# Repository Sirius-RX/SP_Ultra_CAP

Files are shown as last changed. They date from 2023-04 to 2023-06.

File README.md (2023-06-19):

# SP_Ultra_CAP

### 目录

[SP\_Ultra\_CAP](#sp_ultra_cap)

- [目录](#目录)
- [项目所属：河北工业大学\_山海Mas战队	Sirius\_P](#项目所属河北工业大学_山海mas战队sirius_p)
- [最后更新时间：2023.6.19](#最后更新时间2023619)
- [每个文件夹下面都有独立的readme，用以解释目录内容](#每个文件夹下面都有独立的readme，用以解释目录内容)
- [文件目录](#文件目录)
- [简介](#简介)
    - [测试视频：【Robomaster超级电容功能展示（默剧）（最高集成度\&较低成本）】](#测试视频robomaster超级电容功能展示默剧最高集成度较低成本)
    - [外设一览：](#外设一览)
    - [以下为渲染预览图，使用渲染软件keyshot](#以下为渲染预览图使用渲染软件keyshot)
    - [实物焊接图（因为喷了三防漆可能有点影响观感）](#实物焊接图因为喷了三防漆可能有点影响观感)
    - [**项目方案优点**](#项目方案优点)
    - [**项目方案缺点**](#项目方案缺点)
- [硬件框图](#硬件框图)
- [软件框图](#软件框图)

### 项目所属：河北工业大学_山海Mas战队	Sirius_P

	我们是于2022年成立，2023年第一次参赛的新战队，还请各位大佬们多多指教。

### 最后更新时间：2023.6.19

2023.6.19	优化CAN发送&接收程序，功能上加上了缓冲功率的使用，默认锁死在20J；

2023.6.3    更新CAN发送&接收程序；

2023.5.31    更新原理图的采样电阻阻值；

2023.4.29	初始化工程，上传了HARDWARE内容和MATLAB内容，初步完成主页面readme；

2023.4.30	更新了部分设计报告内容（要死了，天天做工）；

2023.5.1	更新Doc中readme，更新SOFTWARE中readme，更新HARDWARE中readme，更新设计报告内容，上传了框图源文件，上传源代码；

2023.5.2	更新部分文档中的错别字；

### 每个文件夹下面都有独立的readme，用以解释目录内容

### 文件目录

**请移步文件目录.txt**

### 简介

##### 	测试视频：[【Robomaster超级电容功能展示（默剧）（最高集成度&较低成本）】](https://www.bilibili.com/video/BV1DM4y127du/?share_source=copy_web&vd_source=c66b5cf402383e929f3b27696605cd3c) 

	该项目用作于Robomaster电容管理，使用单板在7.62cm* 7.62cm*2.5cm（高度主要是有个EC11旋钮有点小高）的超小体积下实现了集成度较高的双向buckboost控制，系统的响应频率高达200kHz。

##### 	外设一览：

-   IPS屏幕接口
-   EC11旋钮
-   蜂鸣器
-   RGB灯（三路PWM控制）
-   两路FDCAN通信
-   ICM42605陀螺仪

##### 	以下为渲染预览图，使用渲染软件keyshot

	

	

##### 	实物焊接图（因为喷了三防漆可能有点影响观感）

	

	

##### **项目方案优点**	

1.  工作模式能在buck、buck-boost、boost三种不同的工作拓扑之间进行无感切换，使得电路工作效率最大化；
2.  超高集成度，在保证体积的前提下，集成了诸多外设及其电调中心板的功能，使得底盘只需要两个pcb即可实现所有功能，节省了底盘的安装空间；
3.  超多外设使得开发板的功能能在后续工程的推进可以增加更多的功能；
4.  6层板设计，叠层结构：电源-模拟地（包括电源地）-电源-信号-数字地-信号，设计时正面器件只有功率与模拟器件，背面器件只有数字器件，使得pcb设计中所有的地回路均为最短且具有两个完整的参考地平面。两个地之间使用了一个680R@100MHz/4A的磁珠进行单点连接；
5.  在同类方案中最低的成本：电流采样运放使用NCS210RMUTAG（全新2.8774yuan一片，云汉芯城2023.1.19报价，现在好像涨了），电压跟随运放使用NCS20282FCTTAG（两路运放，全新4.61yuan一片，e络盟2023.1.17报价），桥驱使用ADP3110AKCPZ-RL（全新3.43yuan一片，e络盟2023.1.17报价），MOS使用国产HYG025N06LS1C2（60V/170A 全新4.11yuan一片，立创2023.4.29报价），电感使用国产TMPC1707HP-100MG-D（10uH/16.5A/11.8mΩ 全新7.1yuan一片，立创2023.4.29报价）。上述都是buckboost实现的核心组件，也是各大学校最堆料的一些组件，选型仅供参考，报价均按1个购买价格计算，并非梯度价格；
6.  极高的控制频率：PWM控制频率200k，让你体验几乎瞬时的功率响应，实现方式请移步SOFTWARE readme；
7.  拥有众多保护功能，包括不限于：输入过压保护，输入掉压保护，输出过流保护，输出过压保护等；
8.  *这一块板子没有经过任何迭代，初版即为最终版。

##### 	**项目方案缺点**

1.  电流采样使用了采样滤波电路，导致电流采样放大后的电压有线性误差，每个板子需要单独校准电流参数；

### 硬件框图

**使用drawio绘制，HTML（高清矢量图）请移步Doc文件夹**



### 软件框图

**使用drawio绘制，HTML（高清矢量图）请移步Doc文件夹**

软件框图是当时给自己提供代码功能设计思路用的，实际实现的方式可能与框图中有些不一样（PS：因为框图是写代码之间先画的，所以肯定会和实现差比较多，因为我是懒狗就还没更新，等后续有时间了再更新一下）



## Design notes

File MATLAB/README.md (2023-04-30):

# SP_Ultra_CAP

### 目录内容

此文件夹用以存放Simulink仿真文件

### 文件简介

buck_boost.slx：电路buck工作模式时的仿真文件

buck_boost_mix.slx：电路buck-boost工作模式时的仿真文件

### 文件使用环境

Matlab 2023a

### 文件使用方法

文件主要是用来验证设计合理性和调整PID参数，PID参数调整方法如下：

1.  先将系统中输出的变量调整至由一个PID环决定；
2.  选中Simulink库中的PID模型并点开；
3.  打开后点击自动调节栏目中的调节按钮（注意调节方式选择基于频率相应）；
4.  配置好对应的参数之后点击调节，具体参数的含义及其配置方式可以参考Matlab官方教程，链接如下：[Design PID Controller Using Plant Frequency Response Near Bandwidth - MATLAB & Simulink - MathWorks 中国](https://ww2.mathworks.cn/help/slcontrol/ug/design-pid-controller-using-plant-frequency-response-near-bandwidth.html)；
5.  在上述自动调整器输出的结果上微调，直至达到自己认为的理想情况。

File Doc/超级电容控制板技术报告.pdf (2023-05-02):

## 基于 STM32G474 的超级电容控制器

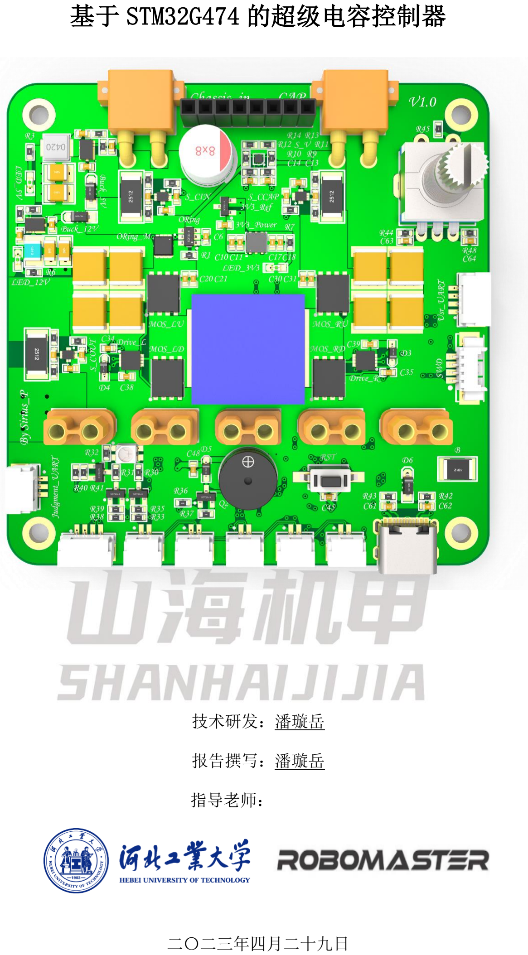
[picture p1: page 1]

技术研发：潘璇岳

报告撰写：潘璇岳

指导老师：

二〇二三年四月二十九日

基于 STM32G474 的超级电容控制器
摘要

针对 Robomaster 赛事中限制兵种底盘功率的规则，本战队制作了一款能够自动控制底

盘输出功率，并合理利用输出功率的超级电容控制器。本设计中的硬件部分主要由一个双向

BUCK-BOOST 变换器及其控制电路构成。包括微控制单元（MCU）、信号采样电路、主拓扑结

构及 MOS 驱动电路、辅助电源电路、传感器电路等。由 MCU 控制输出两路宽度调制的脉冲信

号（PWM）来控制 H 桥中各个 MOS 管导通时间的变化；同时，信号采样电路对输出和输出信

号进行采样，并将其传输给 MCU 来调节系统。系统主要通过 PID 算法来控制功率、电流以及

电压的闭环，更新频率高达 200kHz。经调试，本系统可以根据输出电压，自动变换工作的

拓扑，在 buck 和 buck-boost 工作模式中自由切换，并且在各种情况下都保证输入功率稳

定，最大功率输出可达到 300W。

关键词：超级电容控制器；DC-DC 变换器；PID 算法；

### Abstract

In response to the Robomaster competition's rule that limits the power of certain chassis types,

our team has developed a controller that can automatically regulate the output power of the chassis

and make efficient use of a supercapacitor. The hardware component of this design primarily

consists of a bidirectional buck-boost converter and its control circuitry, including a microcontroller

unit, signal sampling circuit, main topology structure and MOS driver circuit, auxiliary power

circuit, and sensor circuit. The MCU controls the pulse width modulation (PWM) signals that

modulate the on-time of each MOS in the H-bridge to regulate the output power. At the same time,

the signal sampling circuit samples the output and output signals and transmits them to the MCU to

adjust the system. The system mainly employs a closed-loop PID algorithm to control power,

current, and voltage. Through debugging, the system can automatically switch between buck and

buck-boost modes according to the output voltage and ensure stable input power in various

situations. The maximum power output can reach 300W.

Keywords: super capacitor controller; DC-DC converters；PID algorithm

目录

## 1 方案论证

超级电容控制器的硬件主要由一个双向 BUCK-BOOST 变换器构成，裁判系统功率输入经

过理想二极管后与双向 BUCK-BOOST 变换器并联，最后能够与电容放电回路一起输出功率到

负载上。通过改变双向 BUCK-BOOST 中左侧与右侧上管 MOS 给电感的充电时间，可以实现电

流正反向的控制。在系统的调控下，无论输出负载功率如何变化，裁判系统输入功率、能量

缓冲仍符合规则要求，保持稳定。

1.1 | 主控单元的比较与选择
| 方案一：选择数字电源主流方案，使用 TI 旗下的 DSP 芯片作为数字电源控制器，如

TMS320F280x 系列、TMS320F2801x 系列，还有可输出 16 通道高精度 PWM 的 DSP 处理器

TMS320F28044。这些 DSP 处理器开发需要专有的 IDE 并要熟悉其独特的开发方式，学习成本

较高，可能使得工程开发周期较长。

| 方案二：采用 STM32G4 系列。该系列单片机拥有 5 个能达到 4Msps 的 12bit ADC 外设，

外设中使用了专门的加法器电路来实现硬件过采样功能，可以在很大程度上减轻 CPU 负担，

在 ADC 过采样工作模式中可达到 16bit 的精度；有 6 个片上的高速、高增益带宽运算放大器；

7 个能达到 1Msps 的 12 位 DAC（内部输出的话可以达到 15Msps），满足了超级电容控制器

需要精准测量电压电流的需求，同时其 170MHz 的较高主频能有效的提高环路的控制频率。

| 其 HRTIM（高分辨率和复杂波形生成器）外设拥有 6 个独立的 16 位计数器，该计数器

最高能达到 184 ps 的精度，可以生成互补 PWM 波并带有死区控制功能，满足了双向 BUCK-

BOOST 变换器要精准控制 MOS 管导通时间的需求。

| 同时其拥有的 FMAC（数学滤波加速器）外设能够使得 FIR 滤波器或者 IIR 滤波器的计

算完全独立于 CPU，能实现较好的滤波性能同时降低 CPU 的算力开销。

| 但是其价格在贸泽上一片需要 100 多元（2022.12.18，现在淘宝一片也就 40 出头），

实现批量生产成本较高。

| 方案三：采用 STM32F3 系列。该系列单片机具有超快速比较器（25 ns）和可编程增益

的运算放大器。12 位 DAC 以及超快速 12 位 ADC，每通道每秒 5 MSPS（每秒百万次采样），

该系列芯片主频为 72MHz，比 G4 系列的一半还少。虽然其基本满足了超级电容控制器需要

精准测量电压电流的需求，但是在代码实现中较多的计算将会降低系统的实时性。

| 其拥有的 144 MHz 高级 16 位脉宽调制定时器（分辨率 <7ns），可以用于生成互补 PWM

波并有死区控制功能，也基本满足了双向 BUCK-BOOST 变换器要精准控制 MOS 管的需求。

综上所述，选择方案二。

### 1.2 功率检测方式的比较与选择 方案一：数字电流/功率监控器。使用如 INA231 等数字电流/功率监控器，可以通过一

个芯片同时实现双向电流、节点电压以及功率的采集，从而获得校准级别的测量精度以及超

低温漂。这类芯片大多使用I

| 2C通信协议与 MCU 进行数据传输，它在采集完电压电流数值的

同时，能通过内部硬件电路完成功率的计算，并且能直接将该功率数据通过I

2C接口传输给

MCU，能够节省很大一部分的算力开销。同时，这类芯片也可以通过I

2C的配置通过内部硬件

电路完成各个采样值的取平均（等效于低通滤波），也可以编程一个警报阈值，直接通过一

个引脚的高低电平来判断功率是否超过设定值。上述的这些功能在设计上能够将大部分采样、

计算与滤波这些本来应该在 MCU 上完成的功能在传感器芯片上完成，这将能够极大的解放

CPU 的算力，使得系统的响应速度能够更上一层，或者能够将多余的算力来完成其它功能的

设计。尽管如此，这类传感器芯片有几个致命的缺点：1.笔者遍历了 ADI 和 TI 公司的此类

芯片，他们的采样频率基本都不能超过 30kHz，再算上滤波对于采样频率的开销，根据采样

定理可得系统的控制频率也不能超过 30kHz；2.此类芯片一般价格高昂，对于我们这种经济

实力不怎么强的战队来说是一个很大的负担。

| 方案二：运放采样电流电压。通过采样电阻加差模放大器的经典电流采样电路来实现电

流采样。这样的方案相对于上面的方案来说，需要自己编写程序计算功率，同时还要设计好

运放的外部电路。运放采样对于 MCU 来说，在运放端和 MCU 的模拟端均需要一个足够精准且

电流能够快速变化的基准电压源，对于电路设计来说也就需要一个额外的基准电压源电路，

如果想要采样双向电流的话要又额外需要一个独立的电源电压来提供基准电压，这将使得设

计进一步复杂。不过可以通过加一路输出电流采样，通过输入减输出的方式来计算反向电流

的方法来简化设计以及成本。相对于方案一来说，方案二中使用的运放芯片成本较低。

| 综上所述，选择方案二。
1.3 | 系统电路的比较与选择 方案一：裁判系统与电容通过功率路径管理后向底盘供电 当底盘所需功率小于裁判系统所能提供的最大功率时，裁判系统的功率路径被选中打开，

电容组升压的功率路径被关闭，同时，根据官方主控传回的实时输出功率，数字同步 BUCK

模块可以精确设定给电容组充电的功率（即电流）。当底盘所需功率大于裁判系统所能提供

的最大功率时，裁判系统的功率路径被关闭，电容组升压的的功率路径被选中打开，同时，

数字同步 BUCK 模块将裁判系统所能提供的最大功率全给电容充电，电容组通过自主设计的

具有恒压功能的 LM5122 升压模块，向底盘供电，从而保证输出电压恒定，不会烧掉电调或

低压保护。同时数字同步 BUCK 电源可以精确设定给电容充电的功率，利于实现功率闭环。

功率路径管理是由每路电源串联背对背 NMOS 开关，通过 LM5060 功率控制器实现主动式

功率路径管理，实现主动切换输出电路。而输入功率检测是通过电阻串联分压后由 MCU 的

ADC 直接获得输入电压，采用基于霍尔原理的电流传感器高端采集输入电流（电压电流对应

乘积即为功率值）。

但是，当底盘所需功率大于裁判系统所能提供的最大功率时，系统会存在两级 DC-DC 变

换器，总效率由于为两级效率乘积而特别低。根据官方主控传回的实时输出功率，不仅存在

一定的延时性，而且当电容电压越低时，输入输出电压压差较大，系统效率也会随之降低。

功率路径管理为两路背对背 NMOS 开关，在 NMOS 上有一定的能量损耗。设计中并未做到电机

反动势能量回收，而是将其损耗在 TVS 管上。

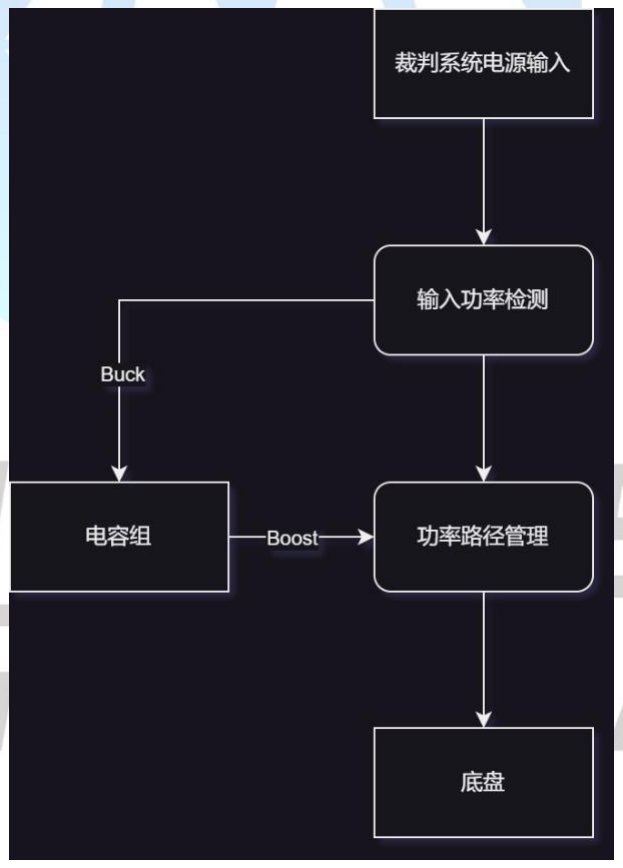
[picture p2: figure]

图 1 系统方案 1 框架简图
方案二：裁判系统通过理想二极管与电容通过双向 DCDC 向底盘供电

当底盘所需功率小于裁判系统所能提供的最大功率时，根据电池端口测量电压、电流得

到的实时输出功率，数字双向 DC-DC 可以精确设定给电容组充电的功率。当底盘所需功率大

于裁判系统所能提供的最大功率时，数字双向 DC-DC 将电容组升高电压，与裁判系统一起向

底盘供电。通过调节数字双向 DC-DC 及电容组的输出功率，我们可以保证裁判系统能量缓冲

稳定在我们预先设置的数值上下浮动，从而实现了能量缓冲的闭环。

输入输出功率都是用运算放大器进行间接测量：运算放大器将电压等比例缩放至

0~3.3V，也就是 ADC 测量范围内，再由单片机 ADC 引脚进行采集；在双向 DCDC 的输入和输

出均放置1mΩ的采样电阻，同样再用一个1mΩ的采样电阻放在电流流入底盘的一端，采样电

阻两端产生的差分电压通过差分运放放大至一个合理范围内之后被单片机 ADC 引脚采集，经

过对应的电压电流计算式，我们可以换算得到真实的电压、电流值，然后通过大名鼎鼎的

P = U × I公式就能得到功率值。此数据具有实时性，所以在闭环中更有优势。

由于系统只存在一级 DC-DC 变换器（可以工作在 buck、buck-boost 或者 boost 三种拓

扑下），对比方案一，该方案总效率为单级效率，效率可得到一定提升。同时，该系统可实

现电机反动势能量的回收。

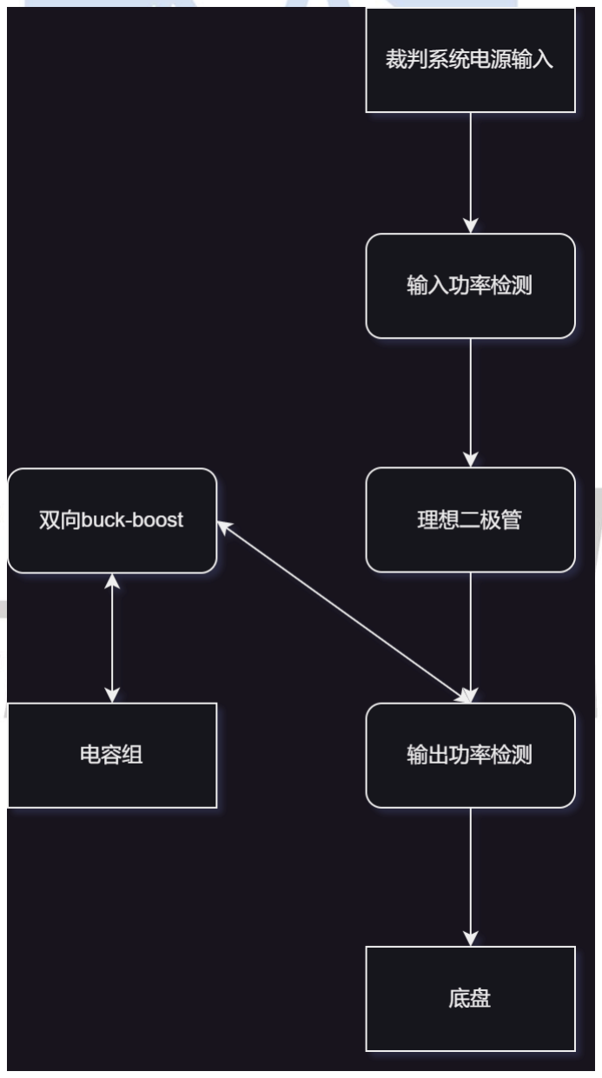
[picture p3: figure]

图 2 系统方案 2 框架简图

综上所述，选择方案二。

### 1.4 方案描述

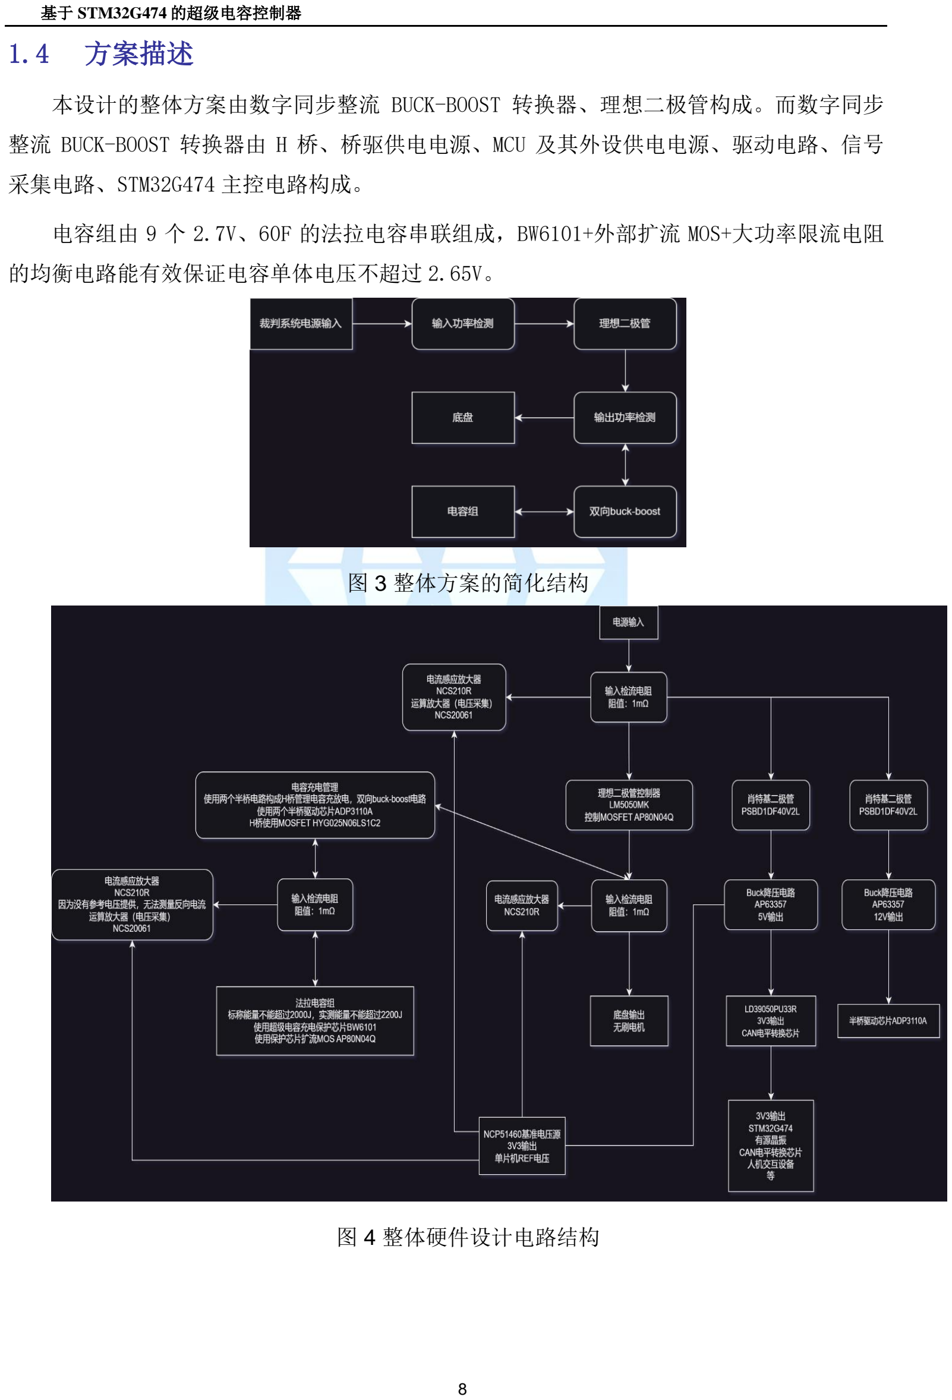
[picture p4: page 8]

本设计的整体方案由数字同步整流 BUCK-BOOST 转换器、理想二极管构成。而数字同步

整流 BUCK-BOOST 转换器由 H 桥、桥驱供电电源、MCU 及其外设供电电源、驱动电路、信号

采集电路、STM32G474 主控电路构成。

电容组由 9 个 2.7V、60F 的法拉电容串联组成，BW6101+外部扩流 MOS+大功率限流电阻

的均衡电路能有效保证电容单体电压不超过 2.65V。

图 3 整体方案的简化结构

图 4 整体硬件设计电路结构

## 2 理论分析与计算

2.1 | DC-DC 变换器提高效率的方法
| DC-DC 变换器效率提升技术主要集中在两个方面：拓扑结构、器件以及控制策略。 拓扑结构及器件上的改进：用 MOSFET 替代经典 BUCK-BOOST 拓扑中的续流二极管，以减

少在其上的压降与功率损耗；同时，选用RDS(on)较小的 MOSFET 和阻值较小的电感以减少导

通损耗；系统电路中尽量减少 DC-DC 转换器数目，保证 DC-DC 变换器两端的输入、输出压差

处在合适范围[3]。

| 控制策略的改进：通过正确设置 MOSFET 开关频率，以减小功率器件开通与关断状态切

换所引起的开关损耗；同时系统会根据输入与输入的电压差，自动判断最优的工作拓扑模式，

例如：在输出电压低于输入电压是右桥上管长时间导通，左桥上下管循环导通，让电路工作

在 buck 模式；在输出电压接近于输入电压时使用 buck-boost 工作模式，这样相对于只用

buck-boost 一个工作模式来说，效率能够得到进一步提高。

2.2 | BUCK-BOOST 控制策略
| 双向同步整流 BUCK-BOOST 电路由同步 BUCK 电路和同步 BOOST 电路级联而成，根据

BUCK 电路电压增益公式：Uo

| Ui = DBU，和 BOOST 电路电压增益公式：Uo
Ui

=

1
1−DBO

推出 BUCK-

BOOST 电路电压增益公式：Uo

| Ui = DBU 1−DBO ，其中DBU定义为 BUCK 电路的占空比，对应本设计中

MOS 管 Q1 的占空比，DBO定义为 BOOST 电路的占空比，对应本设计中 MOS 管 Q4 的占空比。

本设计中 Q1 和 Q2 是一对互补导通 MOS 管，Q3 和 Q4 是一对互导通 MOS 管。双向同步整

流 BUCK-BOOST 电路根据输入输出的电压关系将电路工作状态分为降压区、升压区和降压-升

压区；当输出电压显著小于输入电压时，电路工作在降压区，此时 Q1 和 Q2 互补导通，Q4

常关 Q3 常通，电路等效于同步 BUCK 电路；实际应用中由于 MOS 管驱动采用自举升压的方式，

Q4 不能始终截止，否则当 Q3 的自举电容能量损耗完时，Q3 将截止；为驱动 Q3，Q4 必须导

通一小段时间为 Q3 的自举电容充电以驱动 Q3。因此在实际控制中可将 Q4 的占空比固定设

为 0.75（即DBO可根据实际情况调整），而 Q1 的占空比DBU可在0~0.95之间变化，如此电

路将一直工作在降压区。当输出电压显著大于输入电压时，电路工作在升压区，等效于同步

BOOST 电路，和电路工作在降压区的情况类似，Q2 不能始终截止，需要导通一小段时间为

Q1 的自举电容充电，因此在实际控制中可将 Q1 的占空比DBU固定设置为 0.95（可根据实际

情况调整），而 Q4 的占空比可在0~0.95之间变化，如此电路将一直工作在升压区。当输出

电压和输入电压接近时，电路工作在降压-升压区，即在一个周期内一段时间按降压方式工

作，一段时间按升压方式工作。双向同步整流 BUCK-BOOST 电路 MOS 管开关状态主要有如图

5 所示三种状态。

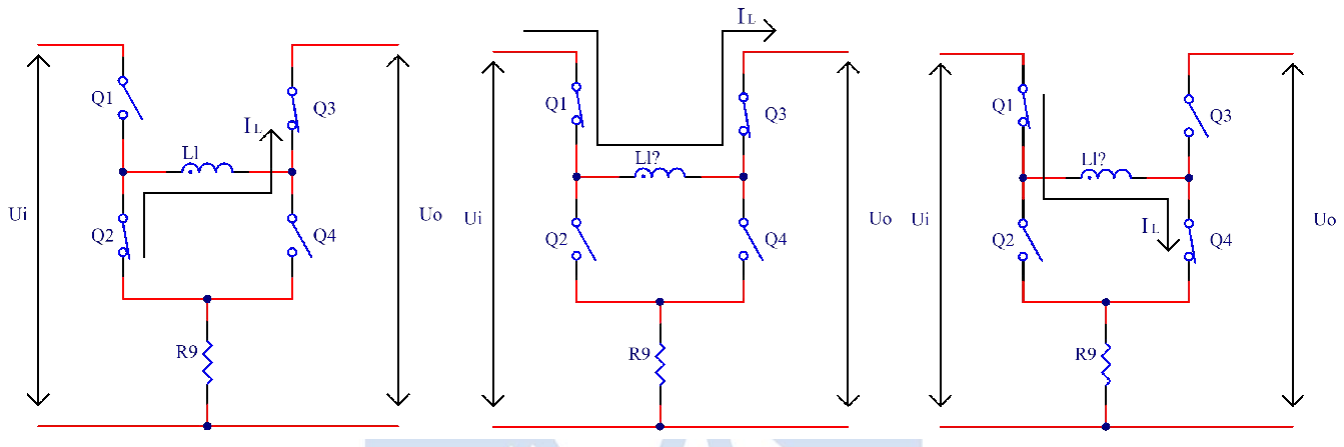
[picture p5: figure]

图 5 MOS 管开关状态

当 MOS 管在 A、B 状态之间切换时，电路工作在降压模式；当 MOS 管在 B、C 状态之间切

换时，电路工作在升压模式；当 MOS 管按照状态 A-B-C-B-A 的顺序切换时，电路工作在降压

-升压模式。如图 6 所示为电路工作在降压-升压模式时的驱动波形和电感电流波形。

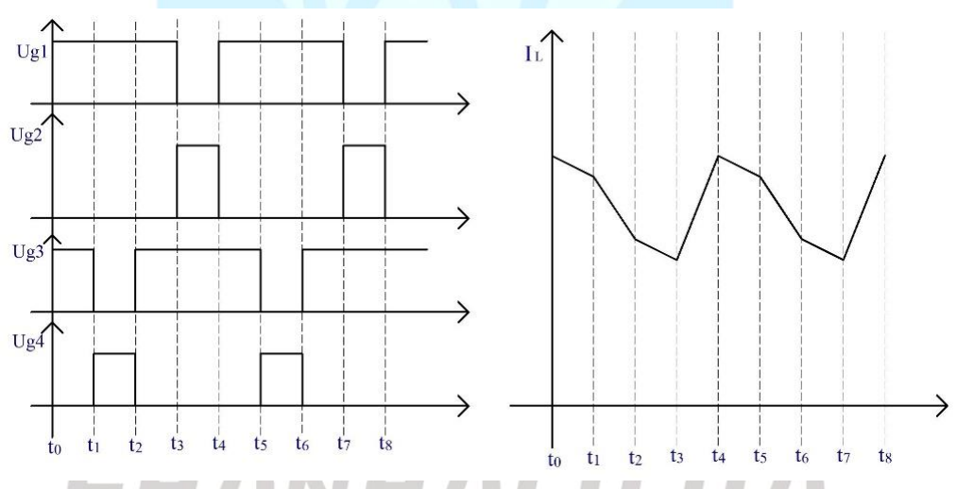
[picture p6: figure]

图 6 降压-升压模式下的驱动波形和电流波形

在t0 − t1阶段电路处于状态 B，此时 Q1、Q3 导通，Q2、Q4 截止；当Ui>Uo时，电感电流

增大；

当Ui < Uo时，电感电流减小。在t1 − t2阶段电路处于状态 C，此时 Q1、Q4 导通，Q2、

Q3 截止，电感电流增大。在t2 − t3阶段电路处于状态 B，在t3 − t4阶段电路处于状态 A，此

时 Q2、Q3 导通，Q1、Q4 截止，电感电流减小。由 BUCK-BOOST 电压增益公式可知，不论电

路是工作在降压模式、升压模式还是降压-升压模式，本质上是控制降压占空比DBU和升压

占空比DBO。

## 3 电路与程序设计

3.1 | DC-DC 变换器主电路与器件选择
| DC-DC 变换器主电路器件为 N 沟道场效应管 HYG025N06LS1C2，驱动芯片 ADP3110AKCPZ-

RL，一体成型电感，插针固态电容和陶瓷电容（MLCC）。

### 3.1.1 DC-DC 变换器主电路设计

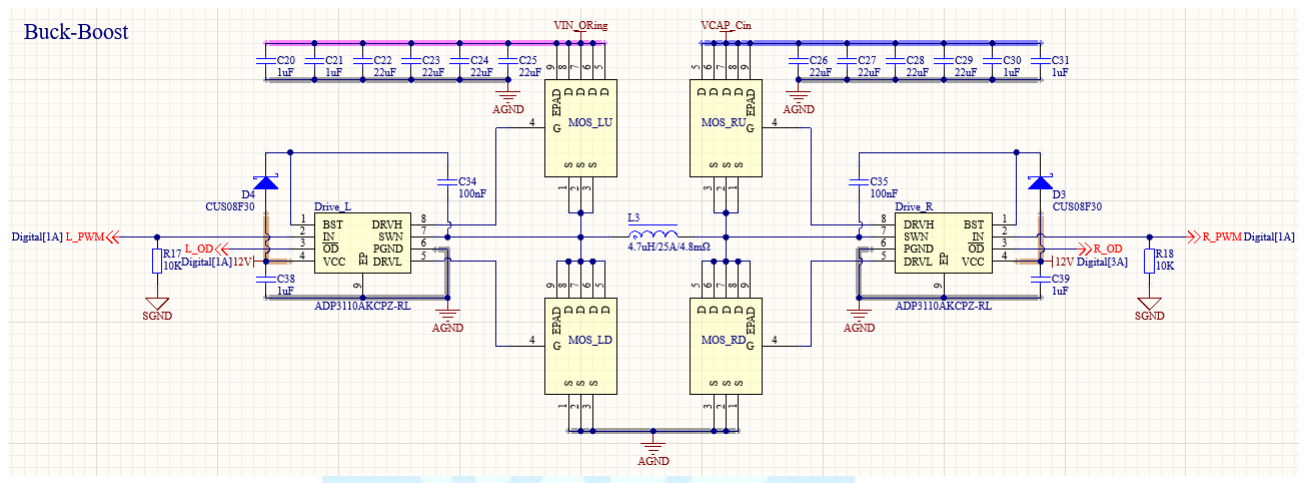
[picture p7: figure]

图 7 双向 BUCK-BOOST 拓扑
由 BUCK-BOOST 参数计算公式可知：纹波系数取 0.3

BUCK 模式需要电感大小：L =

(Vinmax−Vout)D

0.5f×I0utMAX

=

26.2−1
200000×0.3×15

×

1
26.2

= 1.07uH,

BOOST 模 式 下 需 要 电 感 大 小 ： L =

k×Vout(1−D)

2D

2f×I0utmax×10%

=

26.2
200000×2×15×10%

× (

25.2
26.2

)

2 ×

1
26.2

=

6.52uH，

在两种情况取较大的电感值，且留有余量，所以电感 L 取值 10uH。

由于该电路双向对称，所以输入电容和输出电容需要相同容量：

输出最大纹波电压∆UO = 26.2 ∗ 0.3% = 0.0786V,由于使用的固态电容的 ESR 较小，计

算中忽略不计，计算电容充电引起的电容纹波。则所需电容的容值：

C =

∆I
f×∆UO×2

=

0.3×15
200000×0.0786×2

= 143.13uF

输入输出电容要大于143.13uF，不过我们的设计要留有余量。并且需要考虑电机会产

生较大的反生电动势，需要额外的电容来吸收，防止电压的突变。所以最终方案每个半桥的

电源端采用 2 个 1uF/50V X5R、2 个 22uF/50V X7R 和一个 1000uF/35V 8mΩ的固态电容。

### 3.1.2 驱动电路及 MOSFET

MOS 管驱动器采用 onsemi 具有独立的高侧和低侧驱动的半桥驱动芯片 ADP3110A，该

芯片价格低廉，有能够自动产生死区时间的硬件电路，也就是说只需要一路 PWM 便可以控制

一个半桥，简化了控制逻辑。芯片没有集成自举二极管，需要在外部连接自举电容以及充电

二极管，采用自举升压的方式驱动高侧 MOS 管。为了优化效率，这边使用了 30V 1A

230mV@100mA 的 CUS10S30 肖特基二极管作为自举电容充电二极管，自举电容选取 100nF,芯

片驱动电流峰值高达 3A，最大总线电压 35V；在 PWM 信号输入引脚加 10K 的下拉电阻，防

止 PWM 信号输入开路或高阻时 MOS 误动作；MOS 管驱动电阻因为使用的 HYG025N06LS1C2 型

号 MOS 中的RG = 0.58Ω，经计算这个栅极驱动电阻刚好落在不会产生振铃的范围内，故省

略了栅极驱动电阻。

本设计中采用国内公司 HUAYI(华羿微)型号为 HYG025N06LS1C2 的 MOS 管，耐压达 60V，

最大可持续通过 170A 电流，典型小导通电阻3.2mΩ；而本设计中最高电压为 27V,远低于

MOS 管耐压；最大峰值电流为 15A ，也远低于 MOS 管最大持续电流。

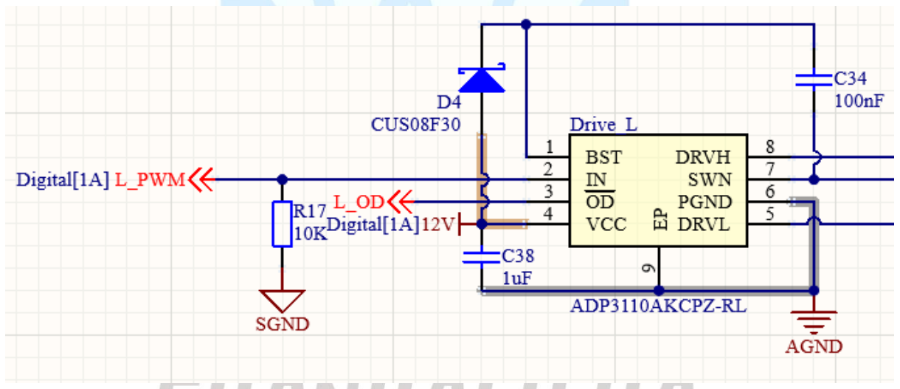
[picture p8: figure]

图 8 驱动电路

3.2 | 信号采样电路
| 输入输出电压通过运放 NCS20282 采用分压跟随电路将输出电压按比例缩小至 ADC 能

够采样的范围，再使用 ADC 采样，软件解算出输出电压。这里的比例使用的是 2.21
2.21+20

=

0.0995，是笔者算遍了电阻表后数据最接近 ¹
10的电阻匹配。输入电压采样是通过 G474 内部

运放作为跟随器再送到 ADC 进行采样的，具体电路如图 12 所示。输出电压检测电路如图 9

所示。

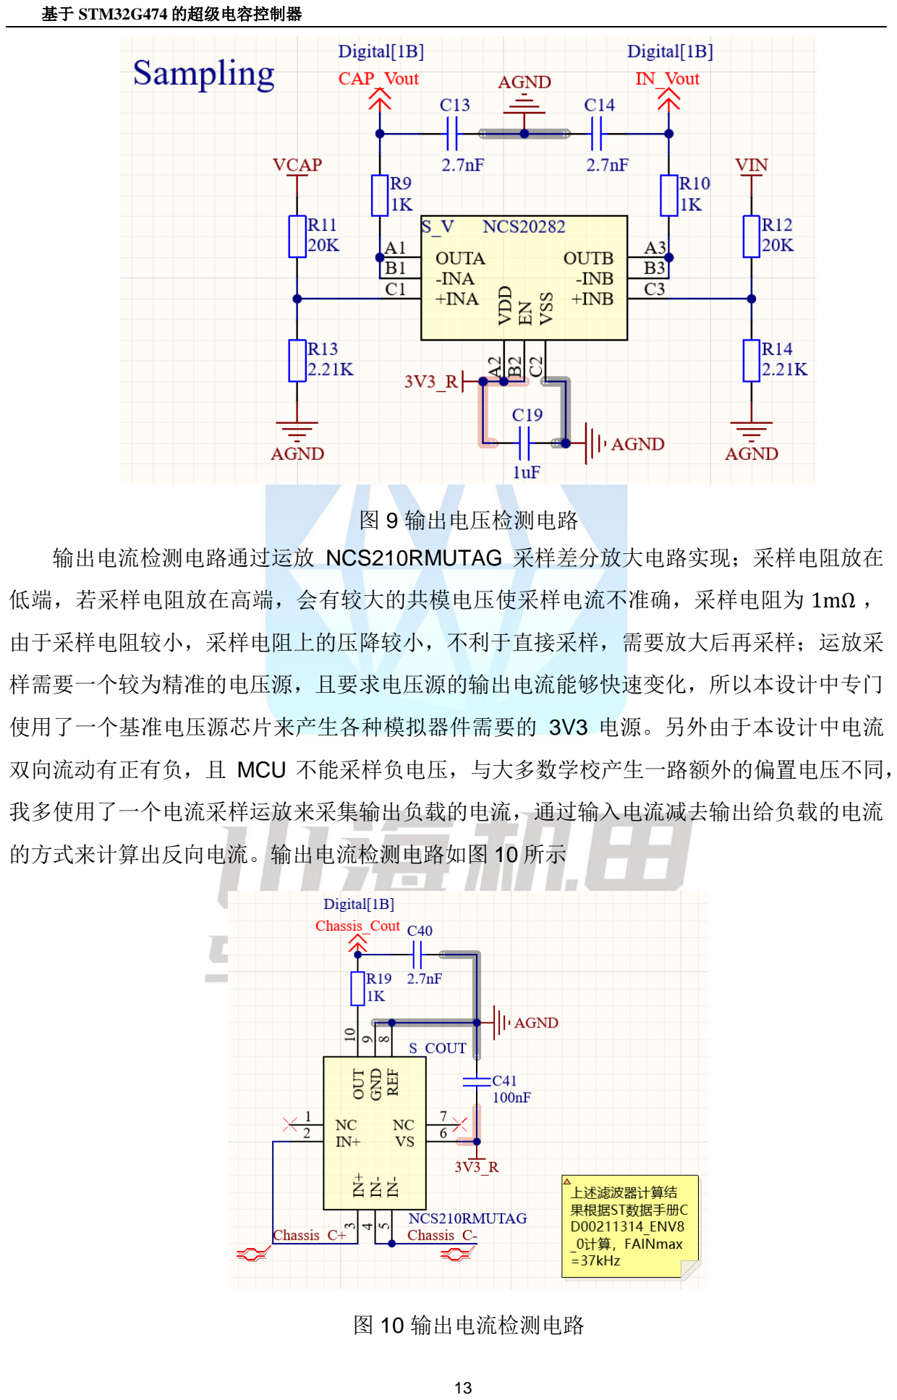
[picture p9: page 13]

图 9 输出电压检测电路
输出电流检测电路通过运放 NCS210RMUTAG 采样差分放大电路实现；采样电阻放在

低端，若采样电阻放在高端，会有较大的共模电压使采样电流不准确，采样电阻为 1mΩ ，

由于采样电阻较小，采样电阻上的压降较小，不利于直接采样，需要放大后再采样；运放采

样需要一个较为精准的电压源，且要求电压源的输出电流能够快速变化，所以本设计中专门

使用了一个基准电压源芯片来产生各种模拟器件需要的 3V3 电源。另外由于本设计中电流

双向流动有正有负，且 MCU 不能采样负电压，与大多数学校产生一路额外的偏置电压不同，

我多使用了一个电流采样运放来采集输出负载的电流，通过输入电流减去输出给负载的电流

的方式来计算出反向电流。输出电流检测电路如图 10 所示

图 10 输出电流检测电路

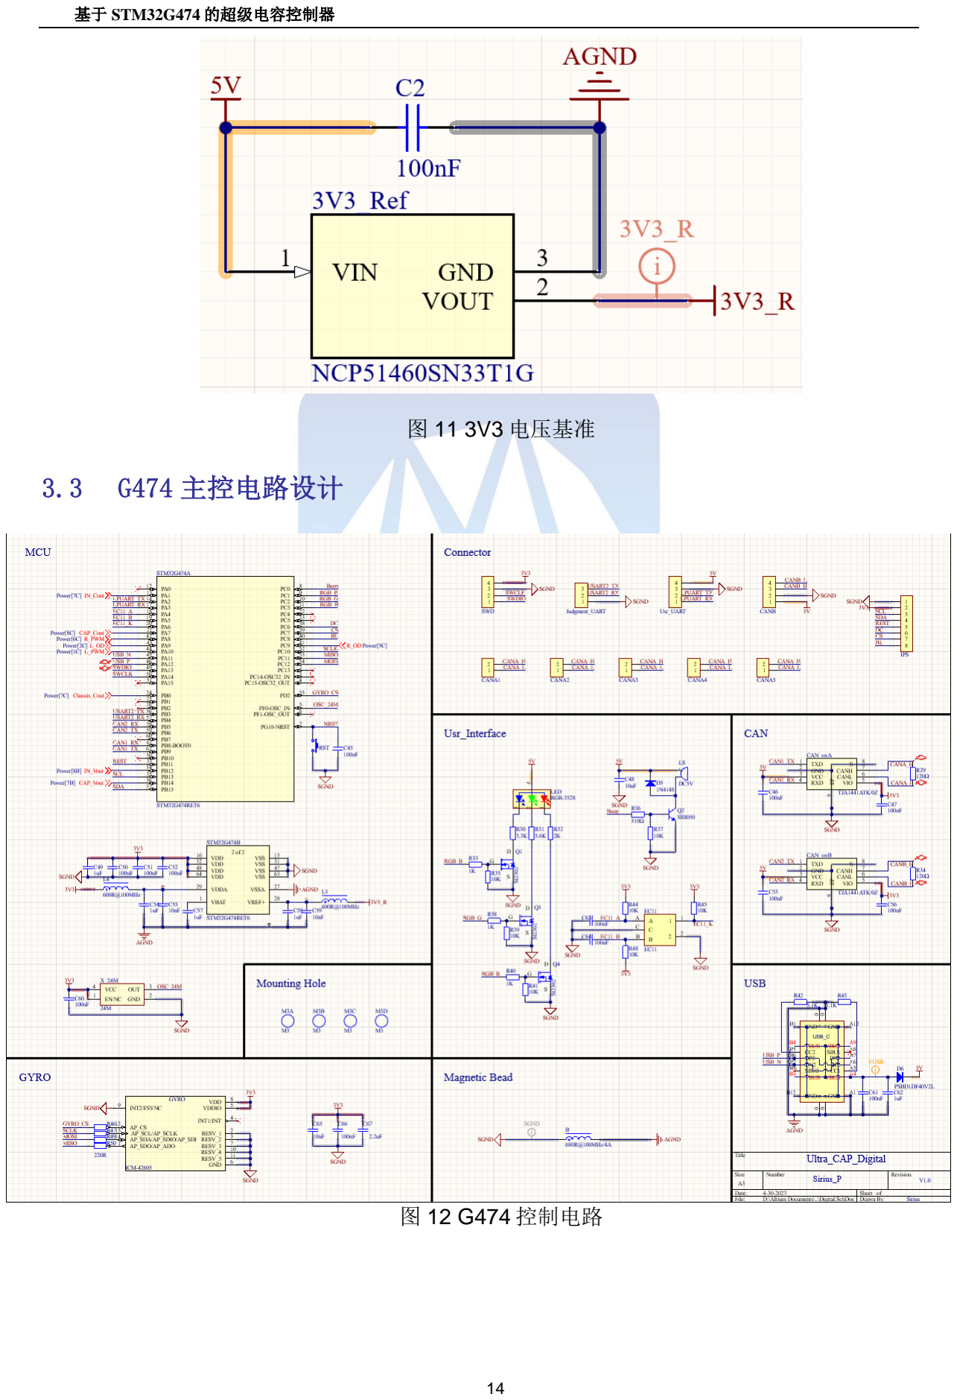
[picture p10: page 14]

图 11 3V3 电压基准

### 3.3 G474 主控电路设计

图 12 G474 控制电路

主控部分以 STM32G474 为主控芯片，预留了串口通信和调试接口，包含了一个 RGB 指

示灯、一个蜂鸣器和一个 EC11 旋钮等外设；G474 引脚分配如下：

信号分类 | 引脚名称 | 对应信号 | 属性
桥驱控制信号 | PA8 | HRTIME_CHA1 | 右桥驱动信号
| PA10 | HRTIME_CHB2 | 左桥驱动信号
| PC9 | R_OD | 右桥驱芯片使能信号
| PB15 | L_OD | 左桥驱芯片使能信号
ADC 信号 | PA1 | c_in | 电池电流
| PB12 | v_in | 电池电压
| PA7 | c_cap | 电容电流
| PB14 | v_cap | 电容电压
| PB0 | c_chassis | 底盘电流
用户串口通信 | PA2 | LPUART1_TX | LPUART1 发送
| PA3 | LPUART1_RX | LPUART1 接收
裁判系统串口通信 | PB3 | USART2_TX | USART2 发送
| PB4 | USART2_RX | USART2 接收
SWD 调试 | PA3 | LPUART1_RX | LPUART1 接收
| PA14 | SWCLK
RGB | PC1 | RGB_R | RGB 红色分量
| PC2 | RGB_G | RGB 绿色分量
| PC3 | RGB_B | RGB 蓝色分量

EC11 | PA4 | EC11_A | EC11 旋钮 A 相
| PA5 | EC11_B | EC11 旋钮 B 相
| PA6 | EC11_K | EC11 旋钮按键
BEEP | PC0 | Beep | 蜂鸣器控制
IPS | PB11 | IPS114_REST | IPS 屏幕复位
| PB13 | IPS114_SCL | IPS SPI 时钟
| PB15 | IPS114_SDA | IPS SPI 数据
| PC6 | IPS114_DC | IPS 数据/命令
| PC7 | IPS114_CS | IPS SPI 片选
| PC8 | IPS114_BL | IPS 背光
GYRO | PC10 | GYRO_SCK | 陀螺仪 SPI 时钟
| PC11 | GYRO_MISO | 陀螺仪 SPI 数据输出
| PC12 | GYRO_MOSI | 陀螺仪 SPI 数据输入
| PD2 | GYRO_CS | 陀螺仪 SPI 片选
CANFD1 | PB8 | FDCAN1_RX | FDCAN1 接收
| PB9 | FDCAN1_TX | FDCAN1 发送
CANFD2 | PB5 | FDCAN2_RX | FDCAN2 接收
| PB6 | FDCAN2_TX | FDCAN2 发送
USB | PA11 | USB_DP | USB 差分高边信号
| PA12 | USB_DM | USB 差分低边信号

表 1 STM32G474 主控引脚分配

3.4 | 超级电容均压电路设计
| BW6101 法拉电容保护芯片是专门针对超级电容串联模组的电容单体过压保护而设计的

一款高性能、低价格芯片。其凭借着性能可靠，电路简单，外围器件小，电压精度高等特点，

被广泛应用于 Robomaster 比赛的超级电容均压板设计中。

| BW6101 采用高精度内部电压基准，确保保护电压精度在 1%以内，内置功率管可以提供

大电流泄放能力，在没有外部扩流管的条件下，可以提供 200mA 的电流泄放能力；如果需

要大电流泄放保护，可以采用外部增加扩流 MOS 管，最大泄流能力可以达到几安培甚至几十

安培，满足大容量法拉电容模组的保护要求。

| 本电路由 9 个 2.7V、60F 的法拉电容串接而成： 其最大电压： Umax = 9 × 2.7 = 24.3V 标称能量：
| E = 9 ×

1
2

CU

2 = 1968.3J

| 由于 2.7V 60F 电容容量大，同时需要大电流进行充放电，这时需要更大功率的泄放电

路才能更好地保证电容单体不过压，进而保护超级电容模组的工作安全。因此，我们采用

BW6101+外部扩流 MOS+大功率电阻的结构。已知 BW6101 内部 MOS 管可靠地泄放电流为 200mA，

所以更大的泄放电流必须通过外部 MOS 来泄放。同时为了防止泄放电流过大，需要几个限流

电阻，笔者选用了 4 个的 10Ω/3W 的合金功率电阻并联来完成。

| 每个单体法拉电容的保护电压是 2.65V，当电容两端的电压大于 2.65V 时，内部泄放开

关打开，通过泄放电阻对下一级电容进行放电，保证电容两端的电压不会过压。

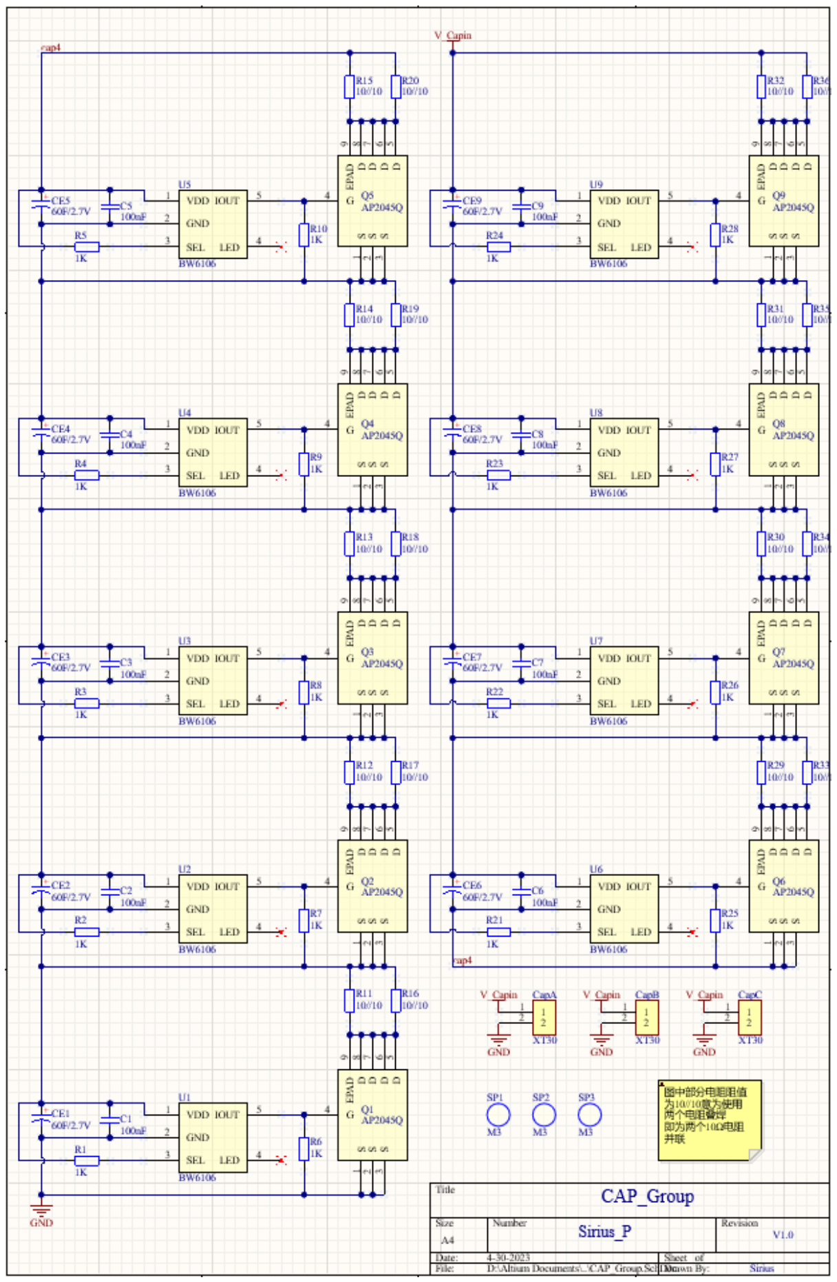
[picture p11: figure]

图 13 超级电容均压板电路图

3.5 | 控制电路与控制程序
| 本系统采用一个双向 BUCK-BOOST 全桥转换器的拓扑，根据负载情况、输入情况和电容

组电压，变换器可以工作在 buck、buck-boost 工作模式，实现对电容组的充放电，在各种

情况下均保证输出裁判系统能量缓冲稳定在固定值，机器人不因底盘超功率扣血。(控制电

路见附图 3 )

### 3.5.1 控制原理及数据通路图

| 超级电容的本质是一个可变功率的负载/电源：

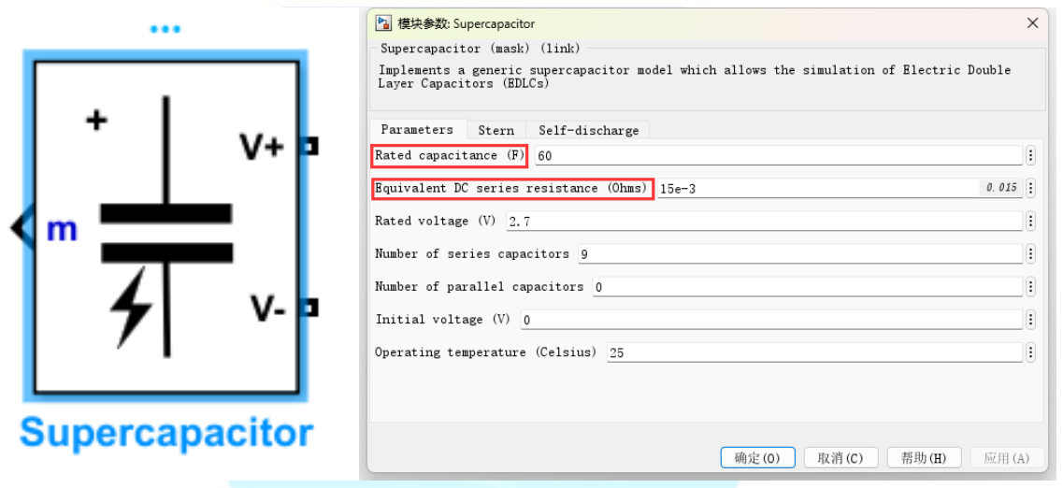
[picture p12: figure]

图 14 超级电容组本质
其中电容可以等效为一个理想电容和一个电阻的串联，当加在电容两端的电压大于或小

于“理想电容”两端的电压时，由于电流流过，电阻两端就会产生压降，进而影响电容的充

电电压。

BUCK-BOOST 模块可以通过改变占空比来改变输入电压或调控输入电流，高效利用裁判

系统所能提供的总功率。

超级电容控制模块能获取的有用信息包括裁判系统传输的底盘限制功率、能量缓冲和测

量得到的裁判系统输出电压、电流，底盘电流，电容组电压、电流。

超级电容控制逻辑主要由三个 PID 构成，它们分别是输入功率环，输出电流环，输出电

压环。

输入功率环的输入数据为测量得到的裁判系统输入电压与输入电流的滤波结果相乘，需

要注意的是输入电流信号是通过 FMAC 外设进行滤波计算。外设数据的装载与读取均使用

DMA 操作，使得输入电流的滤波能够完全独立于 CPU 进程，解放 CPU 算力。输入功率环由输

入数据计算出当前的目标电流值输送给电流环使用，与电流环是串联关系。

输出电流环的输入数据为输出电流采样，因为设计中使用的硬件电路无法测量反向电流，

所以电流放电的电流值是通过计算得出的，计算得出值和实际采样值将会在一个阈值下完成

数据的切换。电流环的输出结果是 PWM 波的占空比，通过调整占空比来实现恒流的功能。

输出电压环的输入数据为电容的采样电压，当电容充电至目标电压时，为了避免电容过

冲导致电容均衡板持续发热（有烧毁风险），在电容电压接近目标电压时需要降低占空比。

电压环的输出为 PWM 波占空比，与输出电流环为并联关系，两环竞争输出最小值。

数据通路如下图：

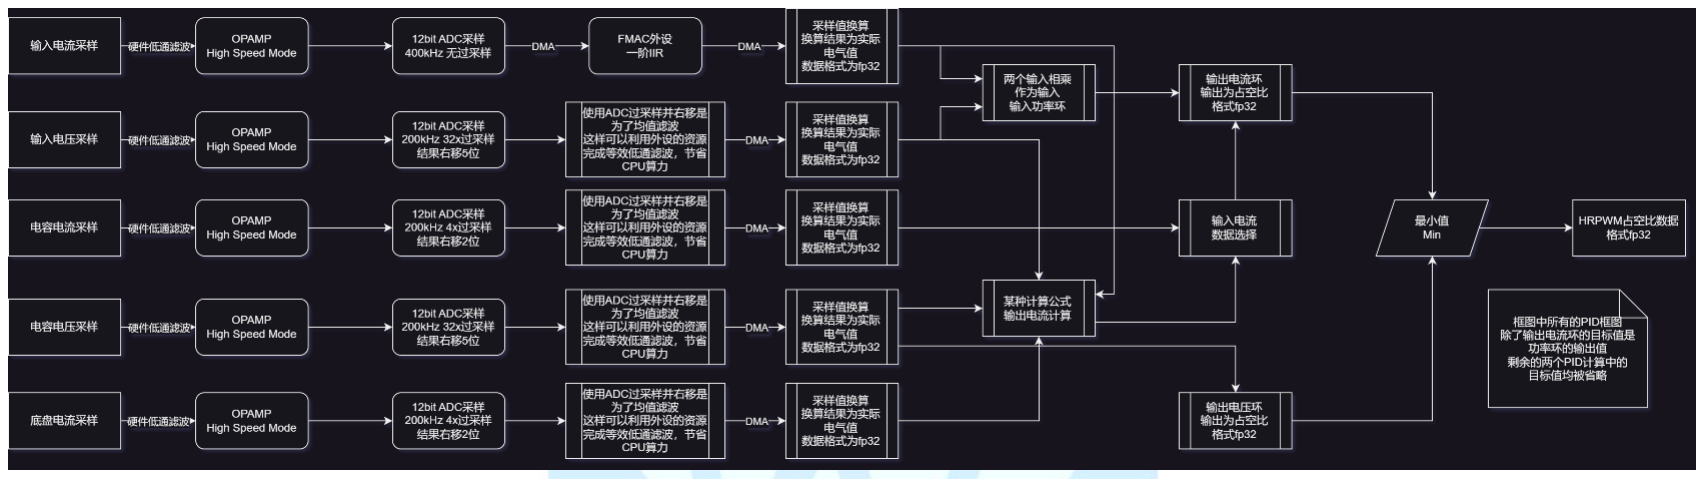
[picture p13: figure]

高清大图请移步于 Github 开源中与此文档同 Doc 目录中的数据通路.drawio.html 文件

图 15 数据通路图

### 3.5.2 程序框架讲解

程序的主要功能包括：

⚫ | HRPWM 输出占空比计算更新
⚫ | 系统错误状态检测
⚫ | 与其它边缘设备 CAN 通信及其数据处理

接下来笔者将分上面三个部分来逐步讲解程序的设计思路

⚫ HRPWM 输出占空比计算更新

通过 200kHz 的 HRPWM master timer 中断执行更新计算程序，数据计算过程可以

参考上图中的数据通路图，输出结果的占空比乘以定时器总 Period 值就能够算出对

应的电平切换定时器值。

同时在 HRPWM master timer 中断中还需要判断当年电路工作的拓扑状态，拓扑状

态等其它工作状态通过 DF 结构体变量存储。

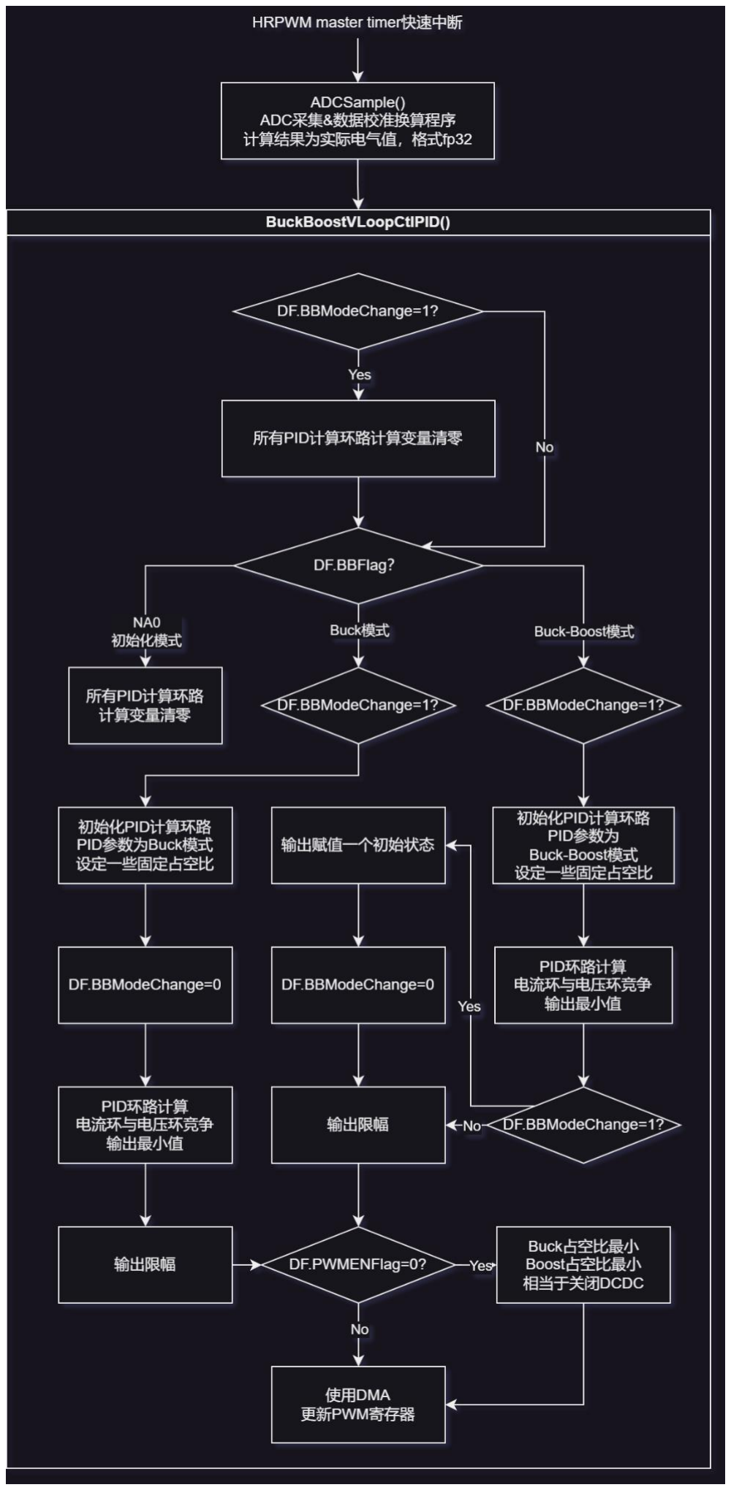
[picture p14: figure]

高清图于 Github 开源中与文档目录中的 HRPWM master timer 快速中断流程图.drawio.html

图 16 HRPWM master timer 快速中断流程图

⚫ 系统错误状态检测

通过 TIM2 定时器的 5mS 中断执行错误状态判断程序以及实现软启动功能，错误状

态包括有短路、输出过流、输出过压、输入过压和输入欠压。

同时在 TIM2 定时器中断中会执行按键检测、电流方向判断（充电或者放电）、工

作拓扑判断以及 RGB 灯颜色的更新，状态更新的逻辑以及判断结果变量请移步至

代码注释，我这边就不一一列出了。

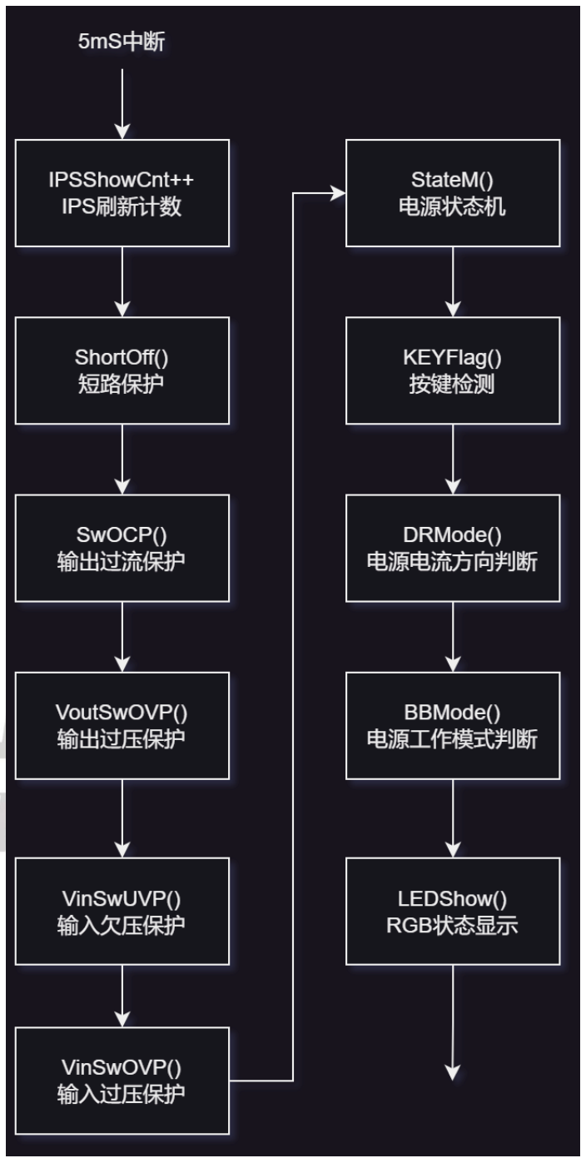
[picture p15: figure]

高清图请于 Github 中与此文档同 Doc 目录中的 TIM2_5mS 中断流程图.drawio.html

图 17 TIM2 5mS 中断流程图

⚫ 与其它边缘设备 CAN 通信及其数据处理

CAN 通信配置了 CAN 滤波器，滤波器条件为固定两个 ID 可以通过，ID 分别为

0x779、0x780。启用了 FDCAN2 的 RX_FIFO0_NEW_MESSAGE 中断，每当

FDCAN2 接收到新的数据包的时候会自动触发中断，中断优先级最低，这样能够保

证 CPU 处理数据效率最高，发送数据包的程序在接受数据中断里头执行，每接收

到一个包返回一个数据包。

这个就不画框图了，再画要累死人了 XD。

### 3.6 测试方案及测试条件

测试设备：RIGOL DS1102Z-E 示波器、APS3010H 稳压直流电源(30V10A)、UTL8212 电子

负载、UT61B+万用表

测试方案：读取稳压直流电源以及电子负载的显示参数完成校准，使用万用表实时监控

电容电压。

### 3.7 测试结果记录

之前测的时候忘记记录数据了，数据一个没有，大三了还得准备考研，懒得再测了。

### 3.8 测试结果分析

通过校正各端口电压电流，可以保证测量数据与真实值误差在 0.05 上下浮动。而整体

系统效率在 95%左右。上车加装裁判系统测试，超级电容控制板响应极快，据操作手反映缓

冲能量条子压根就没动过。

## 4 使用手册说明与注意事项

4.1 | 使用手册说明
| 感觉没有太多需要说明的，这边说明一下 RGB 灯和蜂鸣器的指示状态吧
状态类型 | 指示状态
初始化状态 | RGB 白色 | 蜂鸣器不响
等待软启动状态 | RGB 蓝色 | 蜂鸣器不响
软启动状态 | RGB 蓝&红 = 紫 | 蜂鸣器不响
正常执行状态 | RGB 绿色 | 蜂鸣器不响
错误状态 | RGB 红色 | 哔————

数据包接收格式

ID | 数据域 内容 | 备注
0x779 | rx_data[0] | 裁判系统功率限制参数低八位
| rx_data[1] | 裁判系统功率限制参数高八位
4.2 | 注意事项

### 4.2.1 软件方面注意事项

⚫ printf 重定向了，需要启动 MicroLIB；

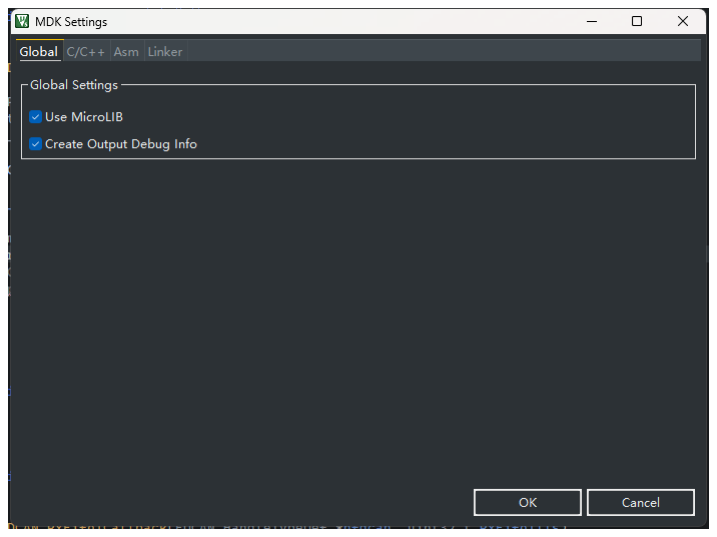
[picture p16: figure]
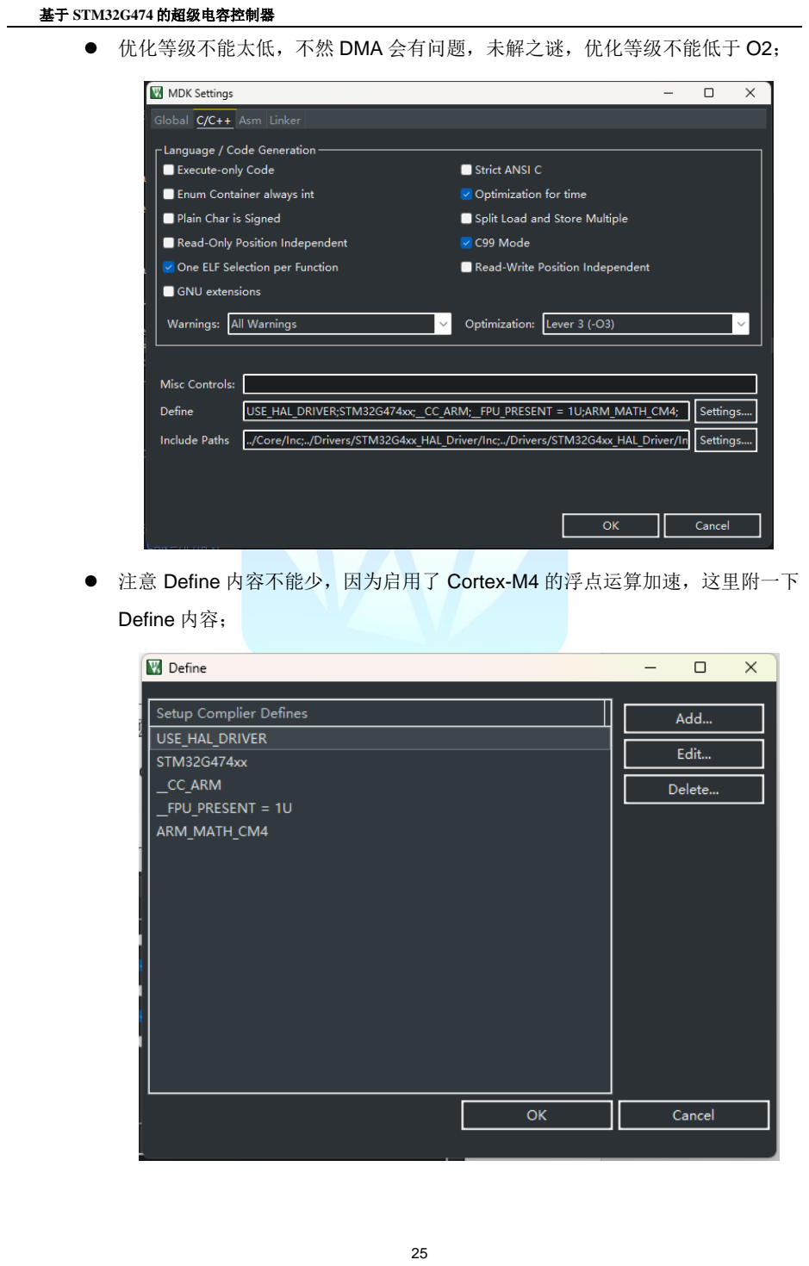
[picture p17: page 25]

⚫ | 优化等级不能太低，不然 DMA 会有问题，未解之谜，优化等级不能低于 O2；
⚫ | 注意 Define 内容不能少，因为启用了 Cortex-M4 的浮点运算加速，这里附一下
| Define 内容；

⚫ | 注意这个工程是有内存分布文件的，因为启动了 STM32G474 的 CCMRAM，
| 将程序存储在这块内存地址上能够加快程序的执行速度。要注意尽量避免将变
| 量存储在 CCMRAM 内存中，因为这块内存在重定向之前只有内核能够访问，
| 外设都不能访问。附一下内存分布文件，字体使用的 Cascadia Code 个人很
| 喜欢这个字体。
| ; *************************************************************
| ; *** Scatter-Loading Description File generated by uVision ***
| ; *************************************************************
LR_IROM1 0x08000000 0x00080000 { | ; load region size_region

ER_IROM1 0x08000000 0x00080000 { ; load address = execution address

*.o (RESET, +First)

*(InRoot$$Sections)

.ANY (+RO)

}

RW_IRAM1 0x20000000 0x00018000 { ; RW data SRAM1

.ANY (+RW +ZI)

}

; RW_IRAM2 0x20018000 0x00002000 { ; RW data SRAM2

; .ANY (+RW +ZI)

; }

ER 0x10000000 0x00008000{

.ANY (ccmram)

}

}

### 4.2.2 硬件方面注意事项

⚫ BGA 封装的那个运放很小，焊接的时候注意别大口呼气，风枪风速也别开的太

快，不然你这辈子也别想找着；

⚫ 后续补充

## 5 总结与展望

超级电容控制板的 PCB 为六层板，在集成了电调中心板的前提下尺寸仅为76mm ×

76mm，为机械极大地节省了空间（即便是这样还是被机械嫌弃太大了）。通过合理的布局

及良好的走线（走了我三个通宵）等，保证了其硬件方面的稳定可靠性。同时，PCB 中所

有的功率与模拟器件都在正面，而所有的数字器件都在背面，再加上使用信号-模拟地-电源-

信号-数字地-信号的叠层结构，使得所有的地回路均有一个大的参考平面且所有的地回流路

径均为最短。且较高的效率使得其不需要散热片就能工作在高负载之下，配合着英雄或步兵

成熟的底盘功率算法，使其使用寿命在恶劣的比赛环境下得到显著提高。

在这个设计中，通过输入与输出端的超大电容使得电机的反向电动势能量能够短时的被

储存，实现了大部分反生电动势式能量的利用。

但是，笔者在设计时错误的理解了缓冲能量的定义，以为缓冲能量是使用完便不会再加

上的调控方式，使得设计中没有充分利用缓冲能量多出来的那份功率，还没有将底盘功率完

全压榨。而且在调试过程中，因为 STM32G474 使用的是 FDCAN 外设，在配置过程中接收

官方 C 板传过来的 CAN 信息没有问题，但是在发送时一直出现了数据不对应的问题，这个

问题还并没有解决。这些问题得等笔者考完研之后自行修复，或者由读到这里的各位大佬修

复后再 github 中推送给笔者 Orz。

顺带一提，这个板子从设计之初到现在没有经过任何迭代，初版即最终版。

笔者的联系方式：1716194438@qq.com，还请各位大佬请不吝赐教！

## 一些随笔&致谢

超级电容控制板的设计始于 2022 年的 10 月：彼时，山海 Mas 站队刚刚建队不久，正

处于危急存亡之秋 XD，并且笔者本人在此之前从来没接触过数字电源设计（笔者本职是搞

FPGA 的），再加上整个战队能做硬件设计比较好的成员就我一个，于是扛下了车车中所有

硬件电路的设计和走线的规划。从 0 开始的学习是艰难的，我们战队刚成立不久，没有技术

积累，笔者又没有对应的经验，只能靠自己一步一步的摸索，更别说从建队到联盟赛只有短

短几个月的时间。

主要的设计是在大三的寒假期间内完成的，那段时间除了吃饭睡觉就是看资料，狠狠的

加大班，终于在开学之前完成了原理图 PCB 设计以及代码框架的初步建立。开学之后休息

了一段时间又是猛猛加班完成了代码。

原理图与 PCB 的绘制顺风顺水，主要是在代码开发的过程中状况频出：HRPWM 有一

个比较器值直接给 0x0000 跳过此次 PWM 生成的特性，而且这个特性还只有 HRTIM_CHA

以及 HRTIM_CHB 的第一个和第三个比较器上有，正好我就是用的这两个比较器用以调整

输出占空比，结果一直碰上短路触发保护代码的情况，困扰了我很长时间。最后还是在去天

津滨海新区看海散心的时候在火车上看数据手册的时候发现了这个问题；只能说是功夫不负

有心人了，数据手册原描述如下：

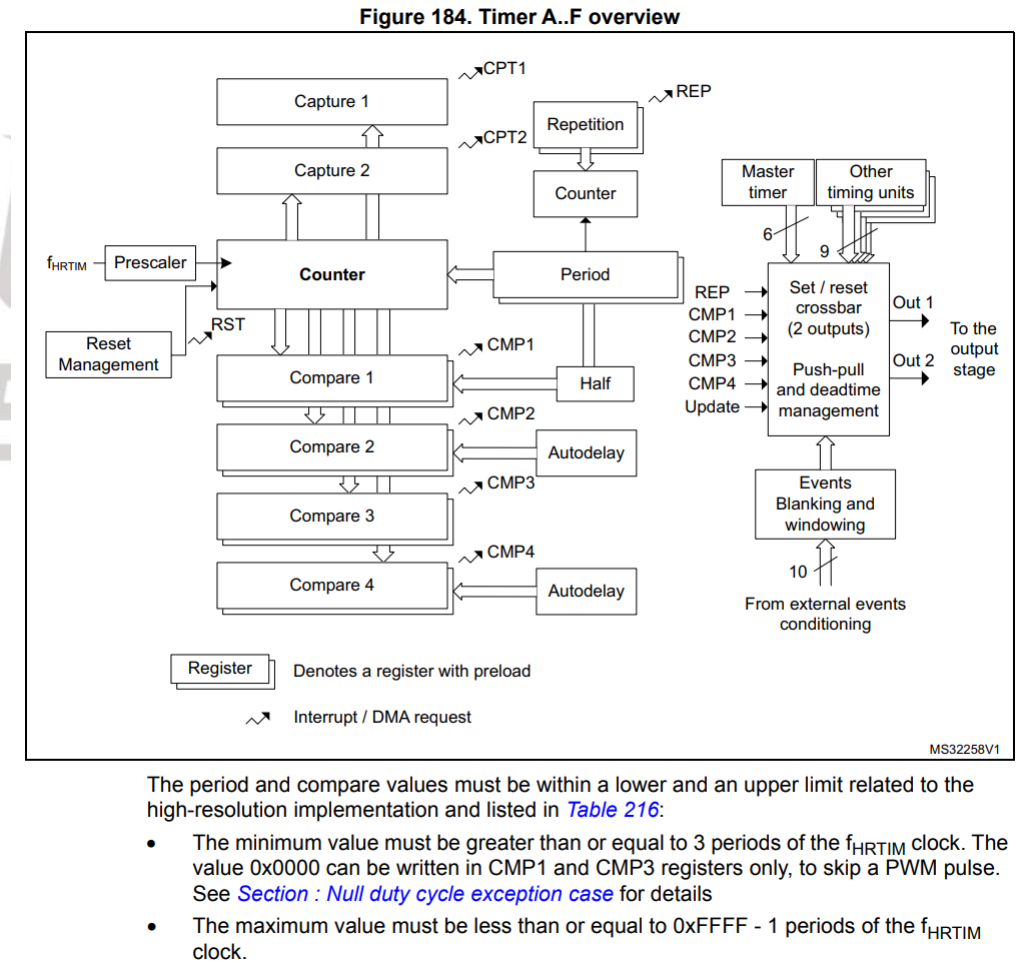
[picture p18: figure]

最小值必须大于或等于 fHRTIM 时钟的 3 个周期。值 0x0000 只能写入 CMP1 和 CMP3

寄存器，以跳过 PWM 脉冲。后来调整了代码解决了这个问题

另外一个情况是输入电流检测的问题，输入电流因为 DCDC 一直工作的原因，采样到

的电流本身就应该是一个跟随开关情况的方波状态，需要对这个方波进行滤波才能得到一个

比较稳定的直流值，仿真示意图如下：

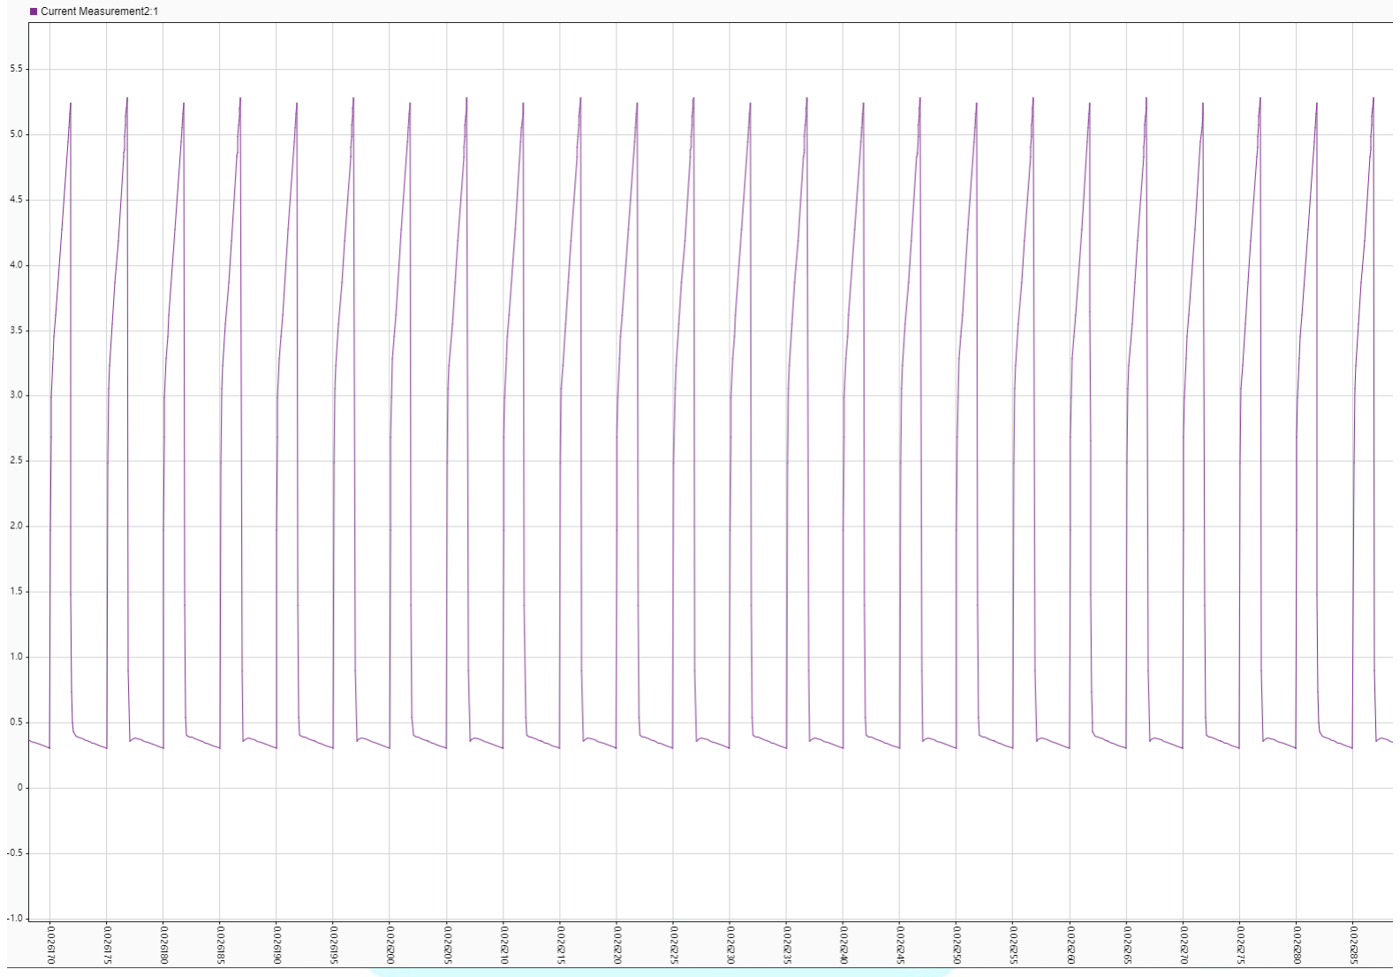
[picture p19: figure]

因为当初觉得使用滤波也能达到这样的效果，再加上带 PWM 抑制器的电流感应放大器

都比较贵，就是用了性价比比较高（垃圾）的运放，然后使用软件滤波的方案。一开始使用

的是硬件低通滤波加传统乘以k(1 − k)的软件低通滤波器，截止频率给到了 100Hz 才能使得

输出的结果保持在一个稳定的状态。但是系统的计算频率是 200kHz，100Hz 的输入信号不

满足采样定理，就一直导致功率环振荡，并且软件低通滤波器一多也导致系统一直卡在

200kHz 中断中（这是执念，就是想用控制频率 200kHz）。后来发现了 FMAC 外设就将输

入的电流滤波使用 FMAC 外设完成了。

说起 FMAC 外设，这里需要特别感谢一下智能车实验室的谷逸明同学。因为 G474 资

料很少，我们配置 DMA 使用 FMAC 外设花了整整一天加一个通宵的时间（我们两个智障搞

错了一个很简单的概念导致一直卡在一个地方）。最后使用了一阶 IIR 滤波，输入电流的采

样频率为了满足滤波导致的频率开销，选择了 400kHz 的采样，最后滤波效果很好，可以看

到测试视频里头的功率环十分稳定，响应也很快。

另外特别感谢一下深圳科技大学的熊泽华，这位老哥在技术上与我有不少的交流，也提

供了一些很好的思路。笔者迄今为止也做过不少竞赛了，但还是被 Robomaster 竞赛开放的

生态所吸引，在这里的大家从不吝啬自己的技术，总是大大方方的拿出来给别人看，这也是

驱动笔者在紧张的考研复习期间完成这份开源报告的源动力。我也想为 Robomaster 的开源

生态献出自己的一份绵薄之力。

最后需要感谢一下在山海 Mas 战队的大家，战队建队的第一年尤其不易，在没有先人

的基础上，每位队员身上都肩负着很多责任。尤其需要感谢我们的队长，在建队初期时我一

度以为我们没有办法真正的迈向赛场，到现在我们第一年参加联盟赛就获得了山东站十六强、

辽宁站十六强的成绩，我对我们队长的领导和沟通能力表示深深的折服。另外也感谢同样身

负重任的其它技术骨干，在我大学生涯的 Last Dance 能这么尽兴也多亏了大家。

最后的最后想说点什么，但是一直又想不出来说点什么，一切尽在不言中了。

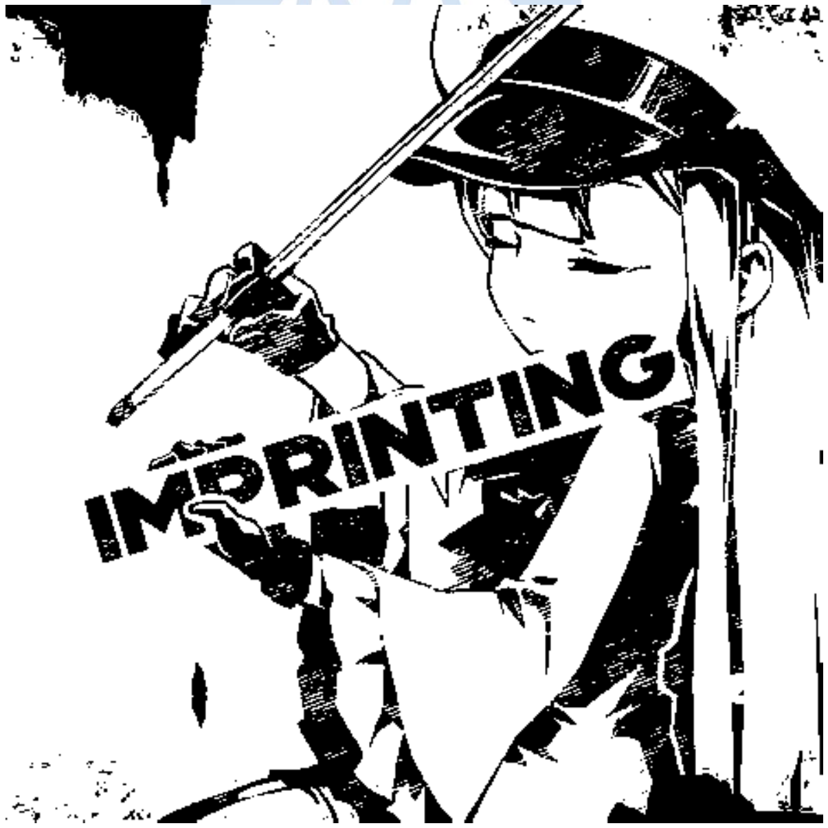
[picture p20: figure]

附件

### 附 1：元器件明细表

电容管理板器件较多，图片比例不适合在 word 文 档 中 展 示 ， 如 需 要 请 移

步./HARDWARE/Ultra_CAP_Ctrl/Ultra_CAP.pdf 文件查看；

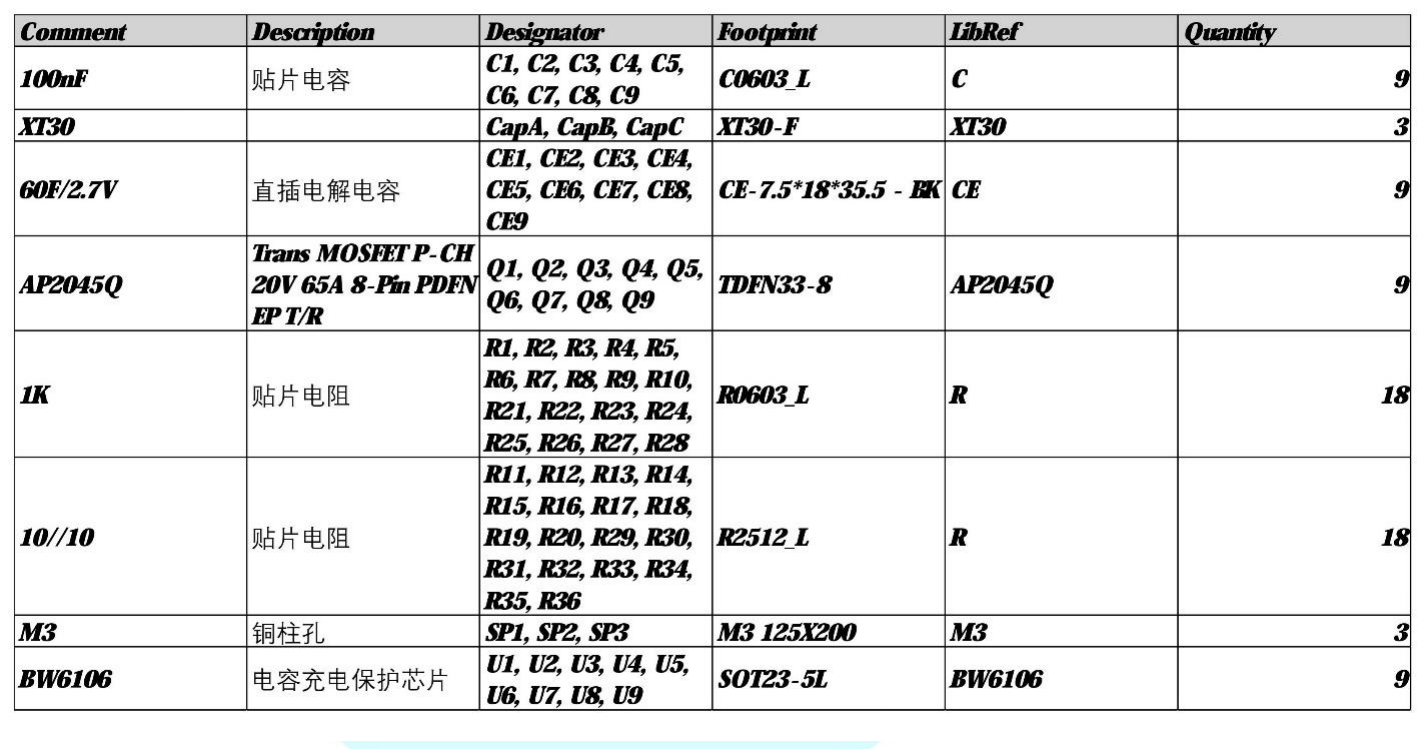
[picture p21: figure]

附图 1 元器件明细表

### 附 2：仪器设备清单

序号 | 仪器 | 数量
1 | 数字万用表 | 1
2 | 二通道示波器 | 1
3 | 30V10A 稳压直流电源 | 1
4 | 300W 电子负载 | 1

附表 1 仪器设备清单

### 附 3：电路图图纸

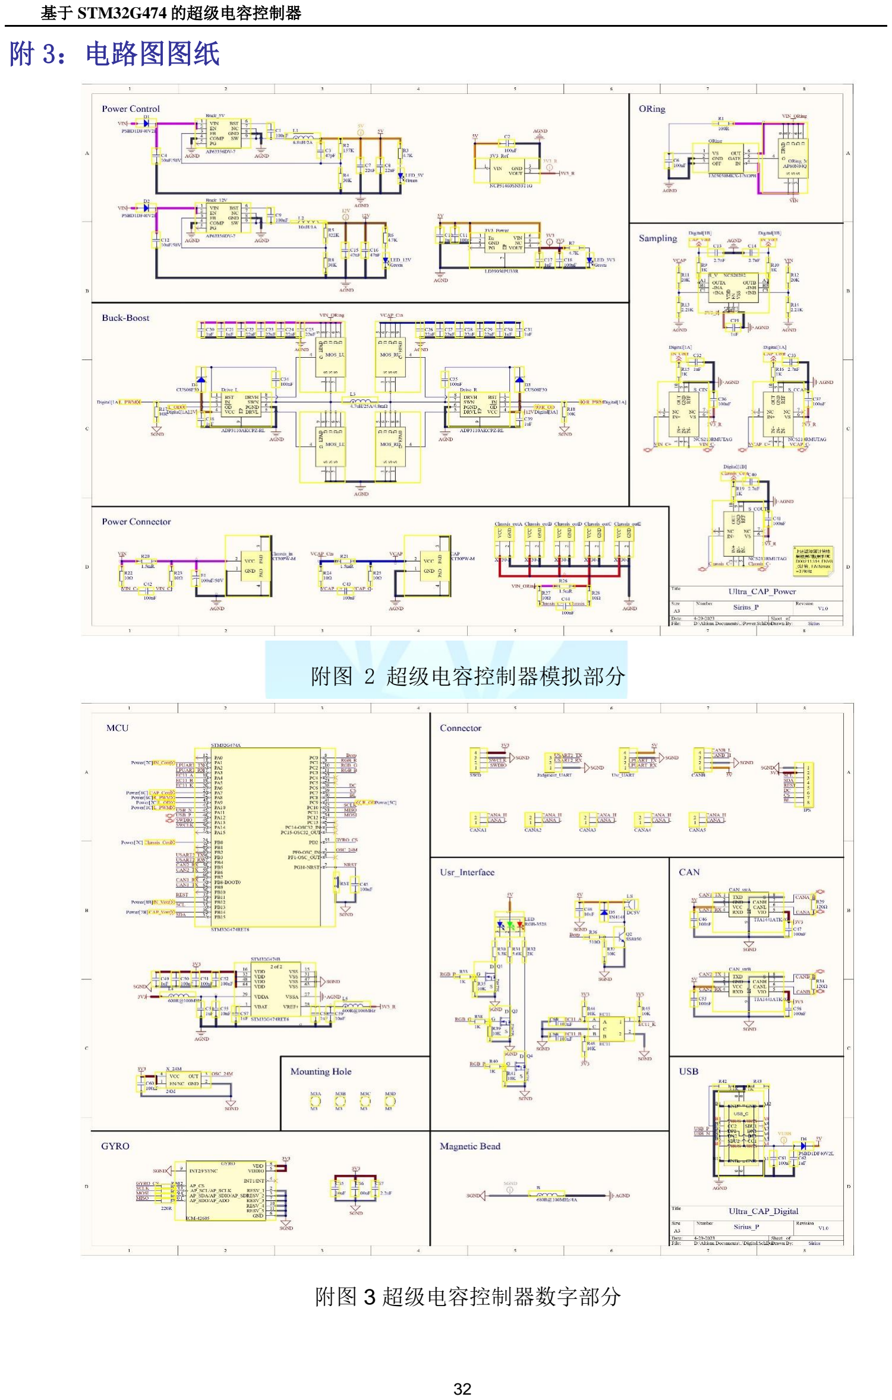
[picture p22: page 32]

附图 2 超级电容控制器模拟部分

附图 3 超级电容控制器数字部分

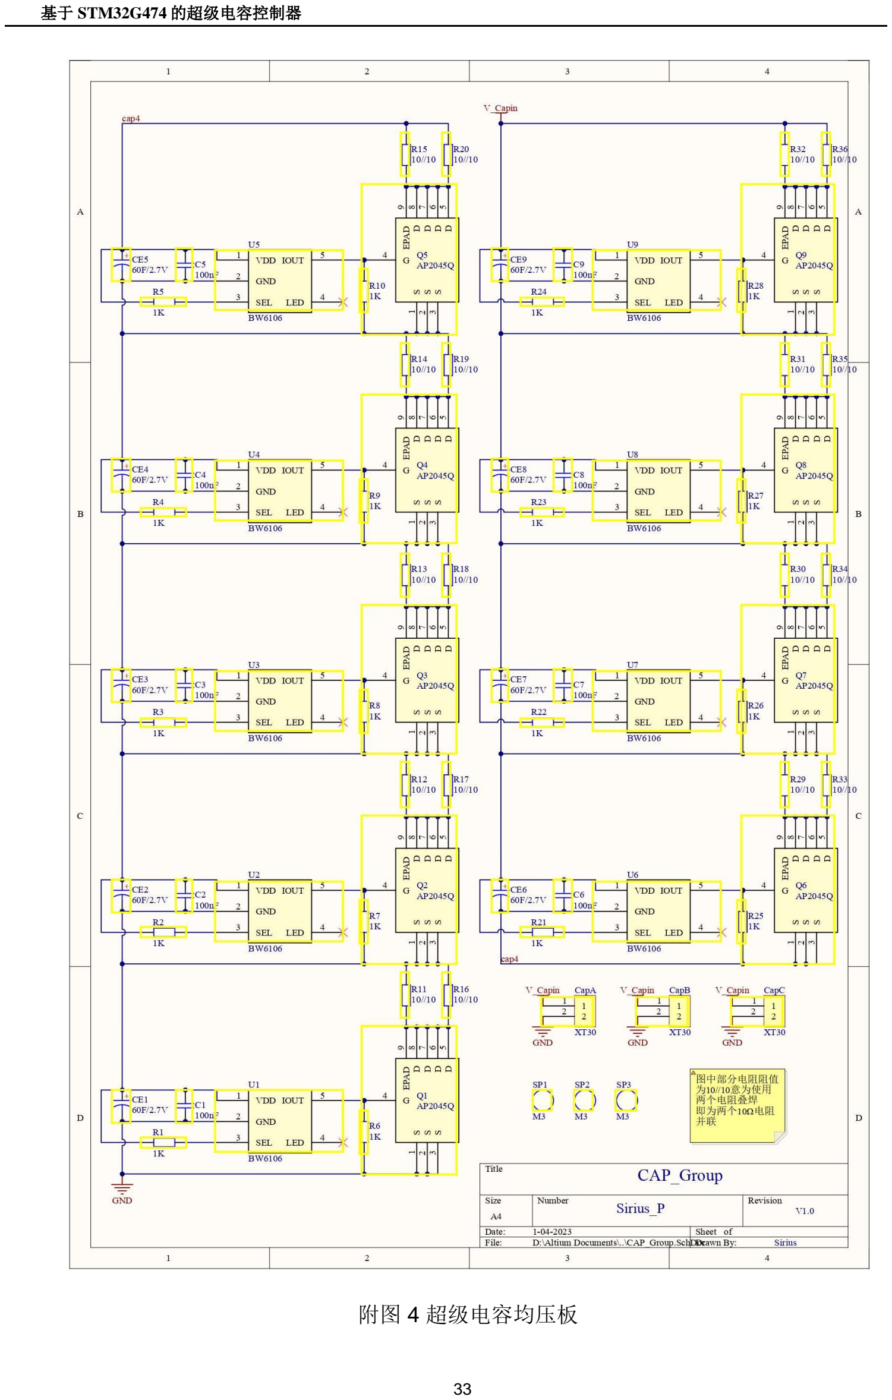
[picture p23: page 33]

附图 4 超级电容均压板

### 附 4：PCB 图

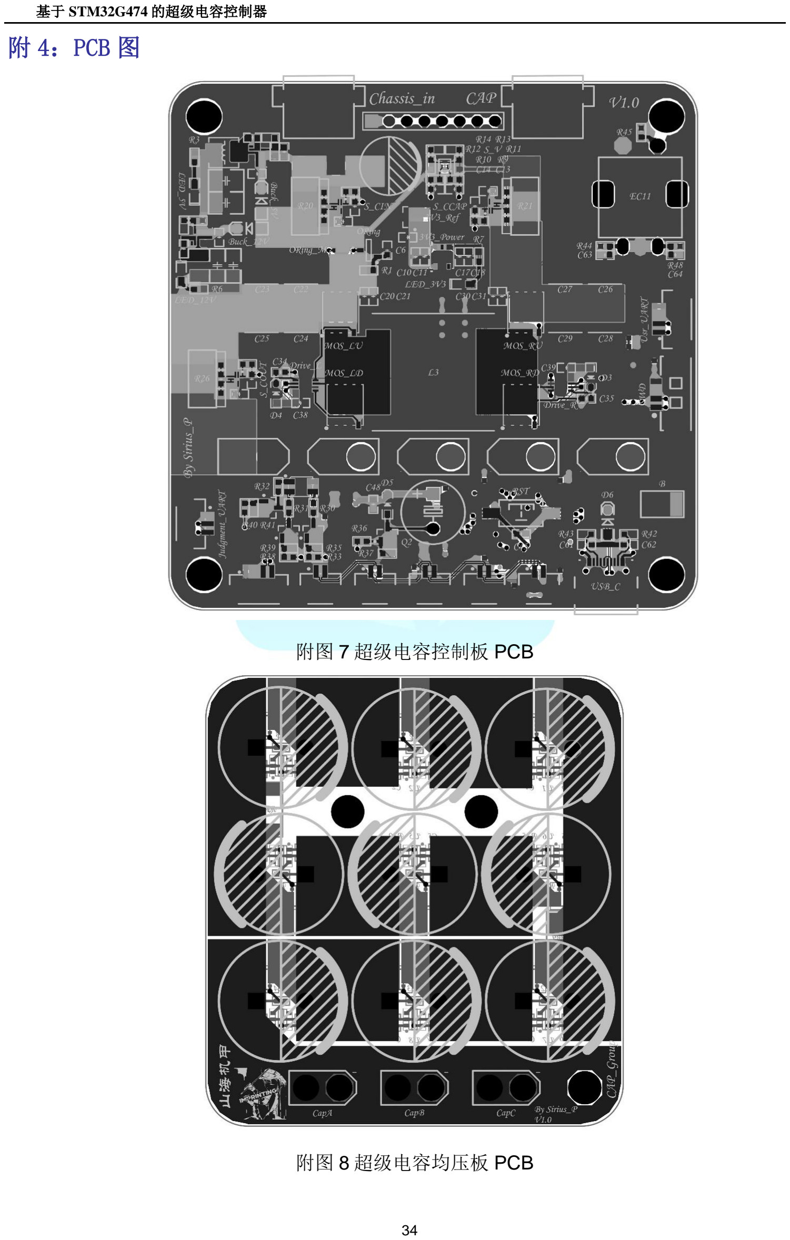
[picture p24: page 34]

附图 7 超级电容控制板 PCB

附图 8 超级电容均压板 PCB

### 附 5：测量数据

都散了吧，测量数据调试的时候没有注意，全没有规范的记录，有也找不到了。不想再

搭测试环境了，原谅我的怠惰。

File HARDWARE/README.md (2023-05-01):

# SP_Ultra_CAP

### 目录内容

此文件夹用以存放Altium Designer工程文件

### 文件简介

GAP_Group：超级电容均衡板

Ultra_CAP_Ctrl：超级电容管理板

### 文件使用环境

Altium Designer23.4.1

### 文件使用方法

这个不用我多说吧，大家本职应该都是搞硬件的，看就完了，具体的设计说明请移步主目录中的Doc文件夹中的技术报告。

如果有什么设计上的疑问的话可以先看看Doc文件夹的设计报告，想要技术交流的话可以通过issue或者通过邮件的方式联系1716194438@qq.com。



附图分别为两个工程的原理图&Layout图

GAP_Group：





Ultra_CAP_Ctrl：







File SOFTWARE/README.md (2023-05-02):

# SP_Ultra_CAP

### 目录内容

此文件夹用以存放超级电容管理板控制代码

### 文件简介

Ultra_CAP内为工程文件夹，请使用Keil或者RT-Thread Studio打开；

代码功能实现方法请移步Doc文件夹查看框图和技术报告，如有未详细描述的部分请根据注释自行理解，不好理解请提出issue或反馈邮箱1716194438@qq.com。

### 文件使用环境

Keil compilerV5.06 update7(build 960)

RT-Thread Studio

### 部分程序框图

高清矢量图请移步Doc文件夹







### 文件使用方法

以下内容摘自Doc文件夹中技术报告的**软件方面注意事项**内容

l printf重定向了，需要启动MicroLIB；



l 优化等级不能太低，不然DMA会有问题，未解之谜，优化等级不能低于O2；



l 注意Define内容不能少，因为启用了Cortex-M4的浮点运算加速，这里附一下Define内容；

 

l 注意这个工程是有内存分布文件的，因为启动了STM32G474的CCMRAM，将程序存储在这块内存地址上能够加快程序的执行速度。要注意尽量避免将变量存储在CCMRAM内存中，因为这块内存在重定向之前只有内核能够访问，外设都不能访问。附一下内存分布文件，字体使用的Cascadia Code个人很喜欢这个字体。

; *************************************************************

; *** Scatter-Loading Description File generated by uVision ***

; *************************************************************

LR_IROM1 0x08000000 0x00080000 {  ; load region size_region

 ER_IROM1 0x08000000 0x00080000 { ; load address = execution address

  *.o (RESET, +First)

  *(InRoot$$Sections)

  .ANY (+RO)

 }

 RW_IRAM1 0x20000000 0x00018000 { ; RW data SRAM1

  .ANY (+RW +ZI)

 }

; RW_IRAM2 0x20018000 0x00002000 { ; RW data SRAM2

;  .ANY (+RW +ZI)

; }

 ER 0x10000000 0x00008000{

 .ANY (ccmram)

 }

}

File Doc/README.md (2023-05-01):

# SP_Ultra_CAP

### 目录内容

此文件夹用以存放工程说明文件；

**drawio源文件**存放所有框图的源文件，方便大家在原框图的基础上直接修改，绘制软件使用drawio；

**STMG474相关数据手册**存放了STM32G474开发相关的官方数据手册，请各位切记数据手册才是开发的基石，当某些外设出现奇怪的毛病的时候请务必通读对应的数据手册内容。

例如HRTIM中如果比较寄存器的值小于某一个主频的阈值将会直接跳过此次PWM生成的特性困扰了笔者调试很久，此外还有一些需要注意的小问题后续更新。

### 文件简介

**数据通路.drawio.html**	对应文档的高清矢量图

**HRPWM master timer快速中断流程图.drawio.html**	对应文档的高清矢量图

**TIM2_5mS中断流程图.drawio.html**	对应文档的高清矢量图

**代码控制框图.drawio.html**	对应文档的高清矢量图

**设计电源拓扑.drawio.html**	对应文档的高清矢量图

**超级电容控制板技术报告.pdf	设计报告矢量图**

### 文件使用环境

PC

碳基生命

### 文件使用方法

用视觉传感器将数据捕捉之后存储进记忆体中，之后将数据通过总线发送给处理器进行数据解析

### 技术报告部分内容预览

		超级电容控制板的设计始于2022年的10月：彼时，山海Mas站队刚刚建队不久，正处于危急存亡之秋XD，并且笔者本人在此之前从来没接触过数字电源设计（笔者本职是搞FPGA的），再加上整个战队能做硬件设计比较好的成员就我一个，于是扛下了车车中所有硬件电路的设计和走线的规划。从0开始的学习是艰难的，我们战队刚成立不久，没有技术积累，笔者又没有对应的经验，只能靠自己一步一步的摸索，更别说从建队到联盟赛只有短短几个月的时间。

		主要的设计是在大三的寒假期间内完成的，那段时间除了吃饭睡觉就是看资料，狠狠的加大班，终于在开学之前完成了原理图PCB设计以及代码框架的初步建立。开学之后休息了一段时间又是猛猛加班完成了代码。

		原理图与PCB的绘制顺风顺水，主要是在代码开发的过程中状况频出：HRPWM有一个比较器值直接给0x0000跳过此次PWM生成的特性，而且这个特性还只有HRTIM_CHA以及HRTIM_CHB的第一个和第三个比较器上有，正好我就是用的这两个比较器用以调整输出占空比，结果一直碰上短路触发保护代码的情况，困扰了我很长时间。最后还是在去天津滨海新区看海散心的时候在火车上看数据手册的时候发现了这个问题；只能说是功夫不负有心人了，数据手册原描述如下：

		最小值必须大于或等于fHRTIM时钟的3个周期。值0x0000只能写入CMP1和CMP3寄存器，以跳过PWM脉冲。后来调整了代码解决了这个问题

		另外一个情况是输入电流检测的问题，输入电流因为DCDC一直工作的原因，采样到的电流本身就应该是一个跟随开关情况的方波状态，需要对这个方波进行滤波才能得到一个比较稳定的直流值，仿真示意图如下：

		因为当初觉得使用滤波也能达到这样的效果，再加上带PWM抑制器的电流感应放大器都比较贵，就是用了性价比比较高（垃圾）的运放，然后使用软件滤波的方案。一开始使用的是硬件低通滤波加传统乘以  的软件低通滤波器，截止频率给到了100Hz才能使得输出的结果保持在一个稳定的状态。但是系统的计算频率是200kHz，100Hz的输入信号不满足采样定理，就一直导致功率环振荡，并且软件低通滤波器一多也导致系统一直卡在200kHz中断中（这是执念，就是想用控制频率200kHz）。后来发现了FMAC外设就将输入的电流滤波使用FMAC外设完成了。

		说起FMAC外设，这里需要特别感谢一下智能车实验室的谷逸明同学。因为G474资料很少，我们配置DMA使用FMAC外设花了整整一天加一个通宵的时间（我们两个智障搞错了一个很简单的概念导致一直卡在一个地方）。最后使用了一阶IIR滤波，输入电流的采样频率为了满足滤波导致的频率开销，选择了400kHz的采样，最后滤波效果很好，可以看到测试视频里头的功率环十分稳定，响应也很快。

		另外特别感谢一下深圳科技大学的熊泽华，这位老哥在技术上与我有不少的交流，也提供了一些很好的思路。笔者迄今为止也做过不少竞赛了，但还是被Robomaster竞赛开放的生态所吸引，在这里的大家从不吝啬自己的技术，总是大大方方的拿出来给别人看，这也是驱动笔者在紧张的考研复习期间完成这份开源报告的源动力。我也想为Robomaster的开源生态献出自己的一份绵薄之力。

		最后需要感谢一下在山海Mas战队的大家，战队建队的第一年尤其不易，在没有先人的基础上，每位队员身上都肩负着很多责任。尤其需要感谢我们的队长，在建队初期时我一度以为我们没有办法真正的迈向赛场，到现在我们第一年参加联盟赛就获得了山东站十六强、辽宁站十六强的成绩，我对我们队长的领导和沟通能力表示深深的折服。另外也感谢同样身负重任的其它技术骨干，在我大学生涯的Last Dance能这么尽兴也多亏了大家。

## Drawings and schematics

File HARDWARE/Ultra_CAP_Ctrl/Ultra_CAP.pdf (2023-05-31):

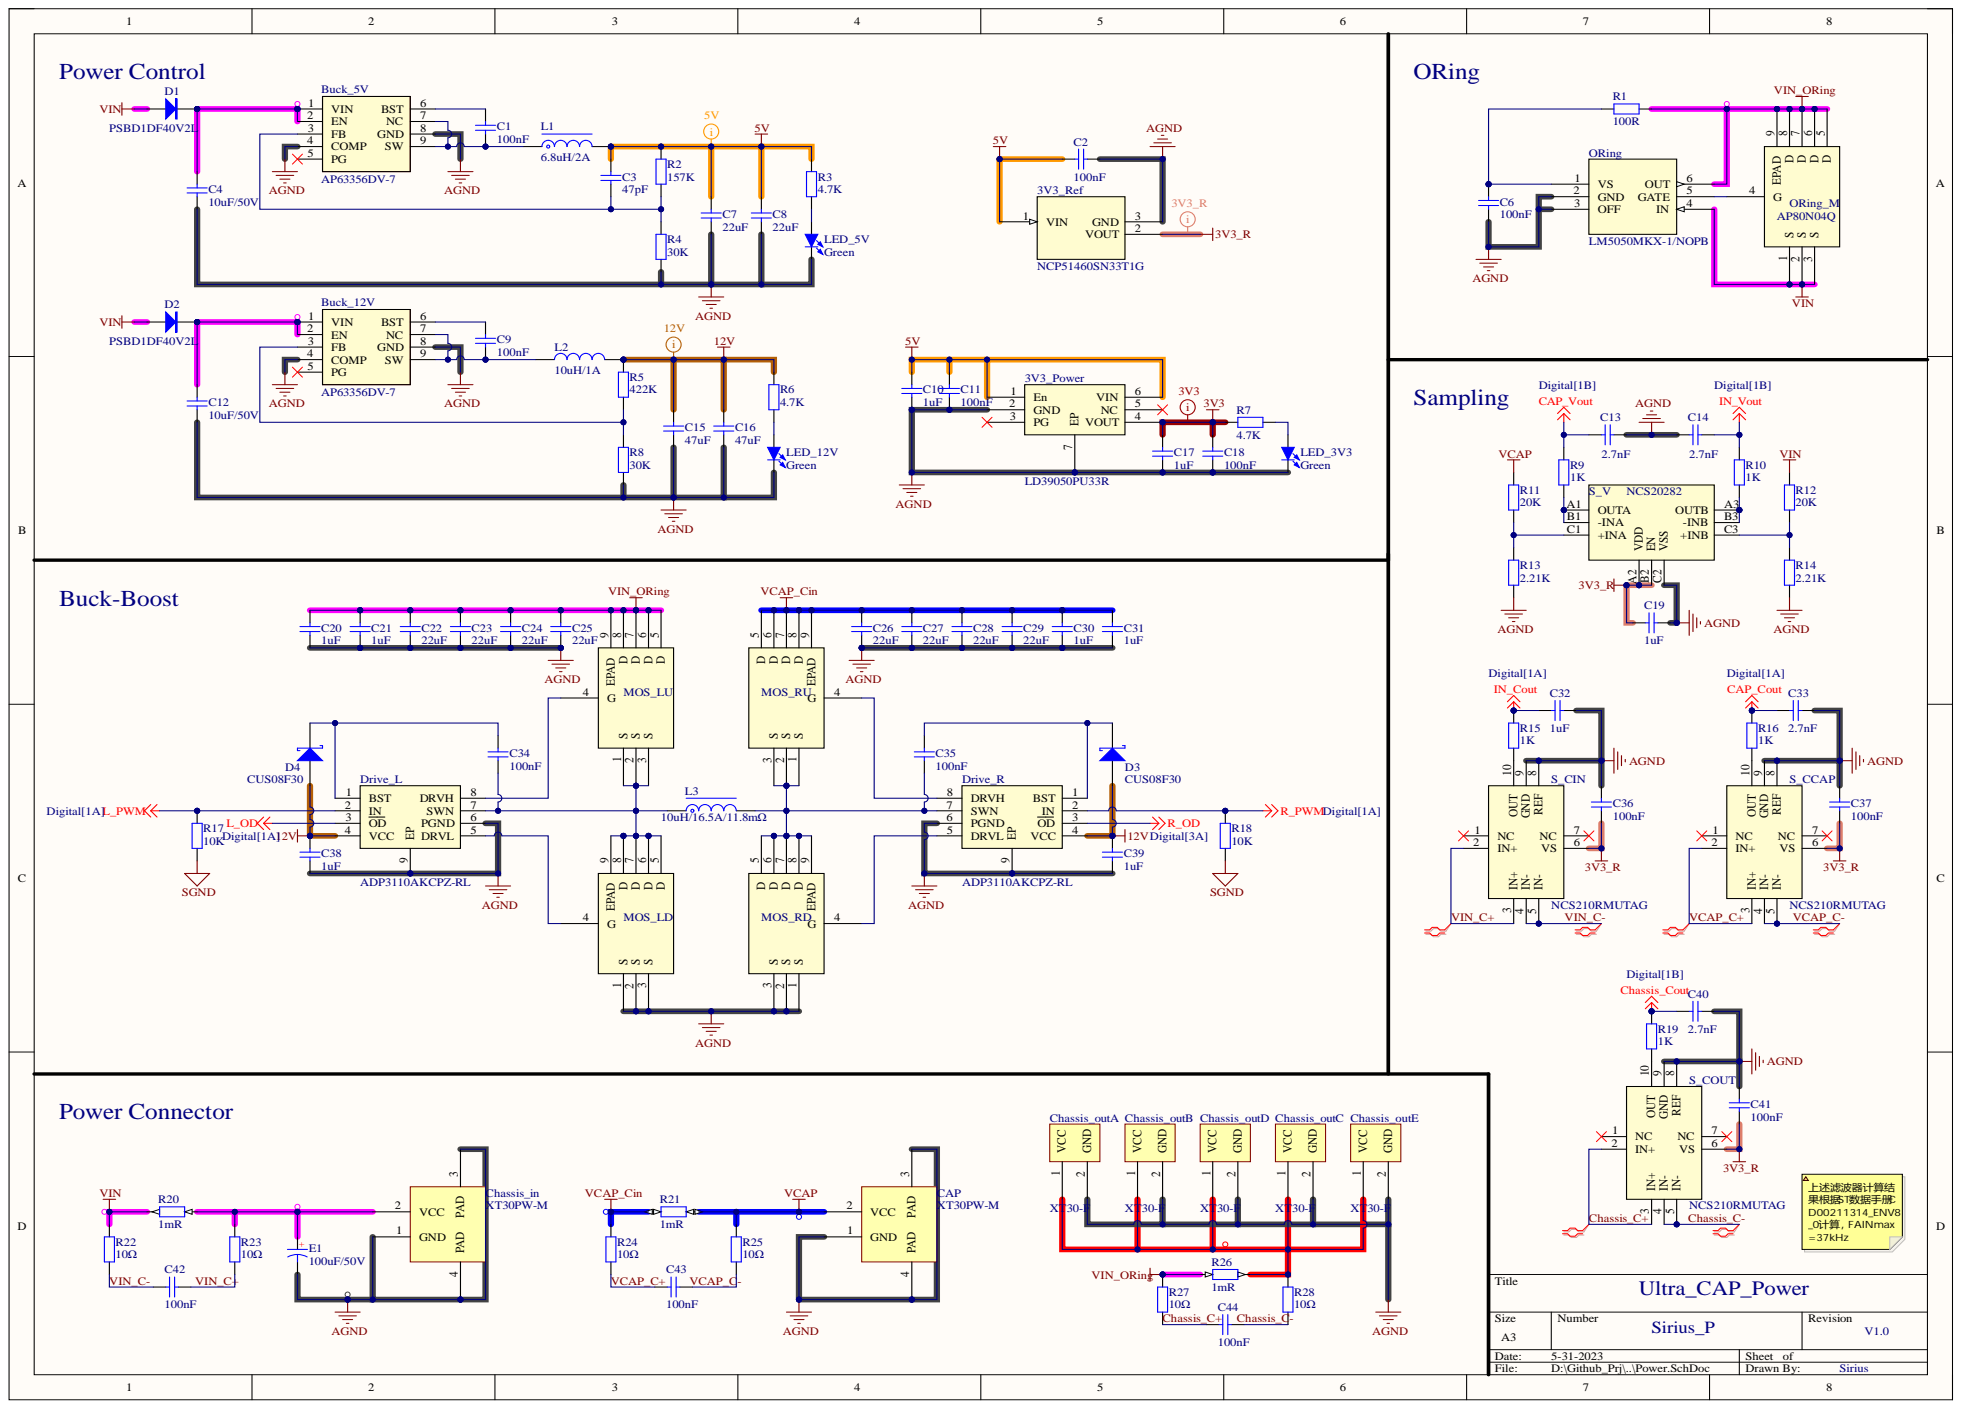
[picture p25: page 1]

S_COUT

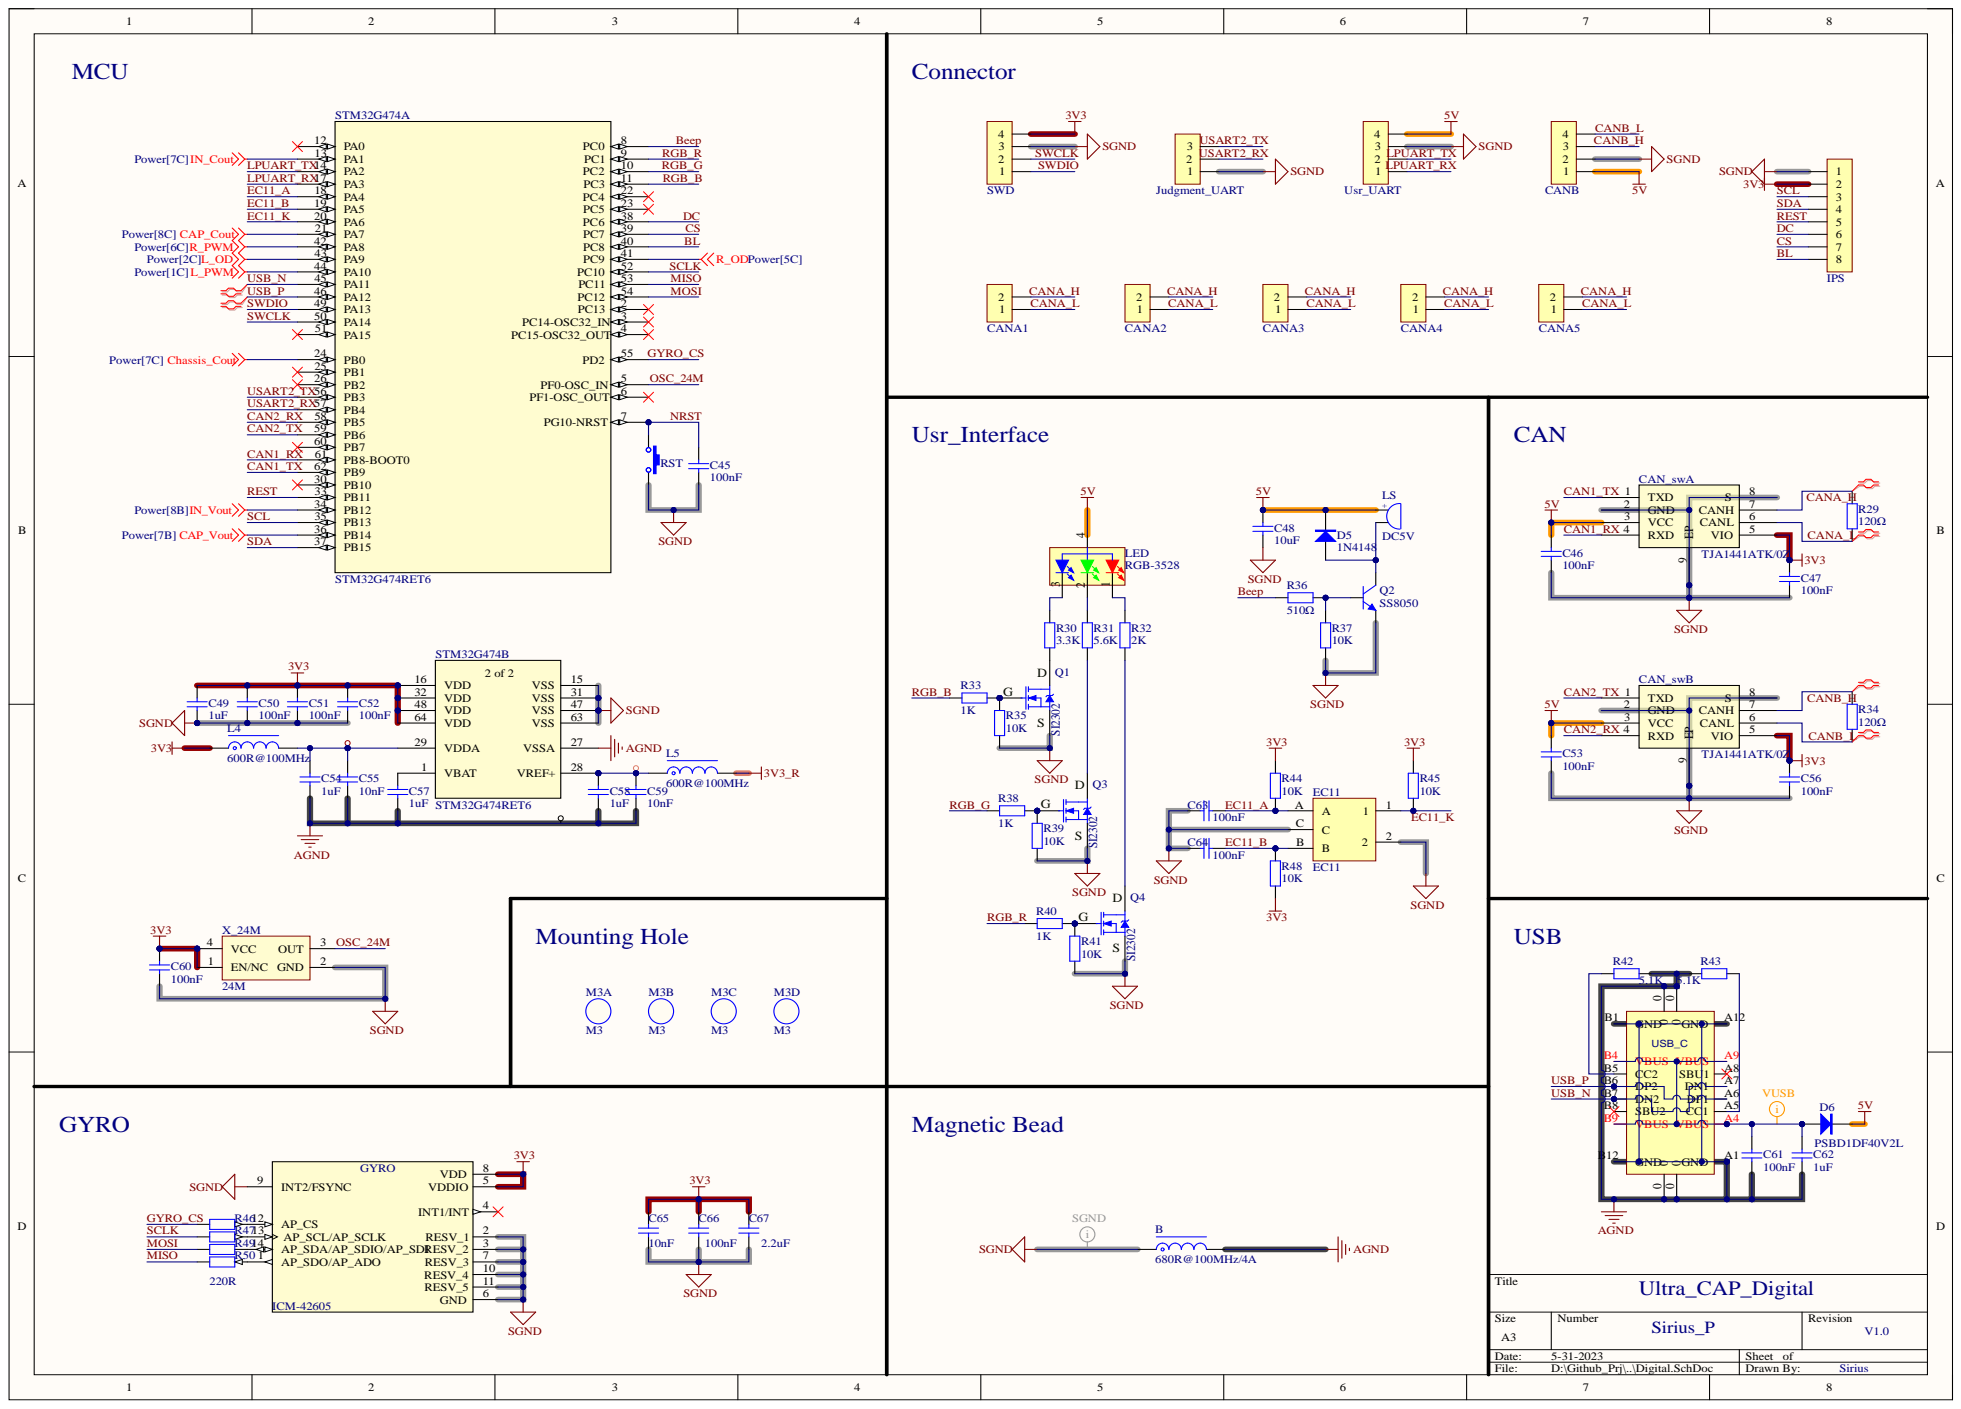
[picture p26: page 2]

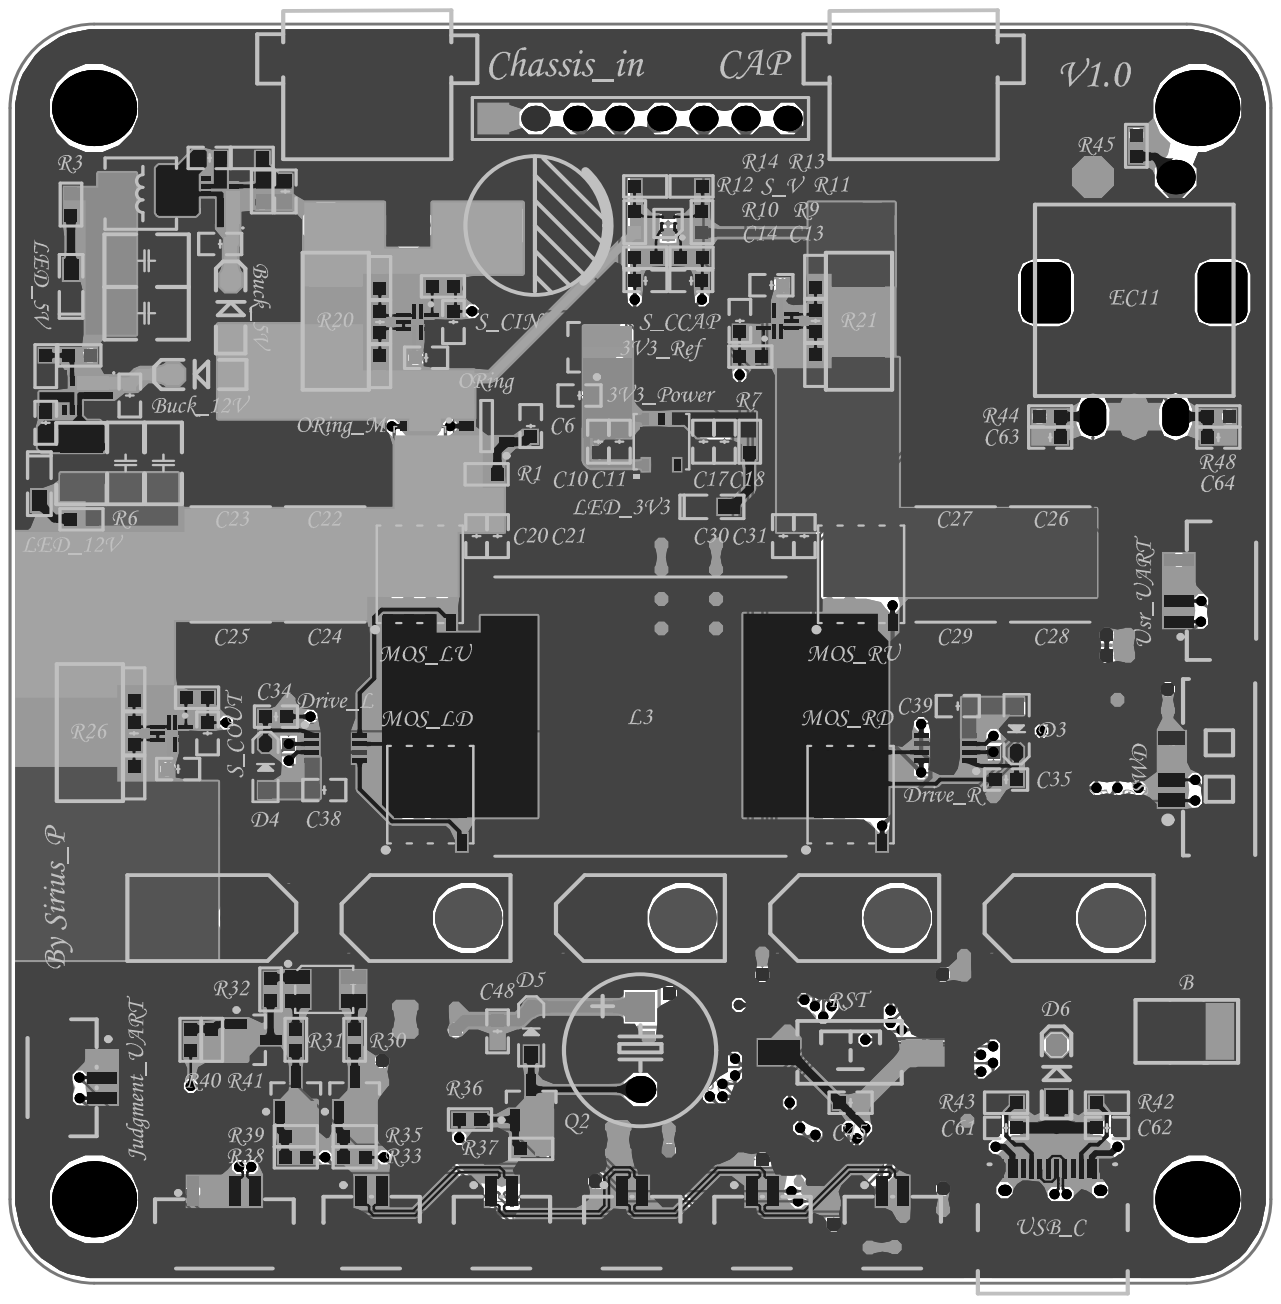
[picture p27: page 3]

Comment | Description | Designator | Footprint | LibRef | Quantity
LD39050PU33R | LDO-3V3/500mA | 3V3_Power | SON_DFN6_3X3_ST M-L | LD39050PU33R | 1
NCP51460SN33T1G基准电压源3V3 | | 3V3_Ref | SOT23 | NCP51460SN33T1G | 1
680R@100MHz/4A磁珠 | | B | R1812_L | FB | 1
AP63356DV-7 | Switching Voltage Regulators DCDC Conv HV Buck V-DFN3020-13 T&R 3K 3.8V TO 32V INPUT, 3.5A LOW IQ SYNCHRONOUS BUCK WITH ENHANCED EMI REDUCTION | Buck_5V, Buck_12V | AP63356DV7 | AP63356DV-7 | 2
100nF | 贴片电容, VDD滤波 电容 | C1, C2, C6, C9, C11, C18, C34, C35, C36, C37, C41, C42, C43, C44, C45, C46, C47, C50, C51, C52, C53, C56, C60, C61, C63, C64, C66 | C0603_L | C | 27
47pF | 贴片电容 | C3 | C0603_L | C | 1
10uF/50V | 贴片电容 | C4, C12 | C0603_L | C | 2
22uF | 贴片电容 | C7, C8 | C1210_L | C | 2
1uF | 贴片电容 | C10, C17, C19, C20, C21, C30, C31, C32, C38, C39, C49, C54, C57, C58, C62 | C0603_L | C | 15
2.7nF | 贴片电容 | C13, C14, C33, C40 C0603_L | | C | 4
47uF | 贴片电容 | C15, C16 | C1206_L | C | 2
22uF | 贴片电容 | C22, C23, C24, C25, C26, C27, C28, C29 C2220_no overlay | | C | 8
10uF | 贴片电容 | C48 | C0603_L | C | 1
10nF | 贴片电容, VDDIO滤 波电容 | C55, C59, C65 | C0603_L | C | 3
2.2uF | VDD滤波电容 | C67 | C0603_L | C | 1
TJA1441ATK/0Z | CAN电平转换芯片 | CAN_swA, CAN_swB | SON65P300X300X1 00-9N-D | TJA1441ATK/0Z | 2
HDR-1X2 | 2P连接器 | CANA1, CANA2, CANA3, CANA4, CANA5 | CONN-SMD_2P-P1.25_JUSHUO_GH1 25-S02DCA-00 | Header 2 | 5
HDR-1X4 | 4P连接器 | CANB, Usr_UART | CONN-SMD_4P-P1.27_GH125-S04DCA-00 | Header 4 | 2
XT30PW-M | | CAP, Chassis_in | CONN-TH_XT30PW-M | XT30PW-M | 2
XT30-F | | Chassis_outA, Chassis_outB, Chassis_outC, Chassis_outD, Chassis_outE | XT30-F | XT30-F | 5
PSBD1DF40V2L | 肖特基二极管 | D1, D2, D6 | SOD-123 | 1N5822 | 3
CUS08F30 | 肖特基二极管 | D3, D4 | SOD-323 | 1N5819 | 2
1N4148 | 开关二极管 | D5 | SOD-323 | 1N4148 | 1
ADP3110AKCPZ-RL | ON SEMICONDUCTOR ADP3110AKCPZ-RL - MOSFET Driver, High Side And Low Side, 4.6V-13.2V Supply, 1A Out, 20n Delay, DFN-8 | Drive_L, Drive_R | SON50P300X300X1 00-9N | ADP3110AKCPZ-RL | 2
100uF/50V | 直插固态电容 | E1 | CT 3.5*8*8 - R | CS | 1
EC11 | 数字开关编码器 | EC11 | EC11 | EC11 | 1
ICM-42605 | Accelerometer, Gyroscope, 6 Axis Sensor IÂ²C, I3Câ„ , SPI Output | GYRO | PQFN50P300X250X 97-14N - duplicate | ICM-42605 | 1
HDR-1X8 | 8P接插件 | IPS | HDR2.54-M-LI-8P | Header 8 | 1
HDR-1X3 | 3P连接器 | Judgment_UART | CONN-SMD_3P-P1.25_JUSHUO_GH1 25-S03DCA-00 | Header 3 | 1
6.8uH/2A | 一体成型电感 | L1 | L-SMD-0420 | L-Molding Choke | 1
10uH/1A | 贴片小功率电感 | L2 | L1210 | L | 1
10uH/16.5A/11.8mΩ | 一体成型电感 TMPC1707HP-100MG-D | L3 | INDPM176169X700 N | L-Molding Choke | 1
600R@100MHz | 磁珠 | L4, L5 | R0603_L | FB | 2
RGB-3528 | 3528三基色LED | LED | LED 3528-4Pin | LED-RGB 3528 | 1
Green | 贴片LED | LED_3V3, LED_5V, LED_12V | LED0603_G | LED-SMD | 3
DC5V | 蜂鸣器 | LS | BEEP 5x9x5.5 | BEEP | 1
M3 | 铜柱孔 | M3A, M3B, M3C, M3D | M3 125X200 | M3 | 4
HYG025N06LS1C2 | NMOS 60V/170A | MOS_LD, MOS_LU, MOS_RD, MOS_RU | PDFN5*6-8l | HYG025N06LS1C2 | 4
LM5050MKX-1/NOPB | 理想二极管控制器 | ORing | SOT23-6 | LM5050MKX-1/NOPB | 1
AP80N04Q | Trans MOSFET N-CH 40V 40A 8-Pin PDFN EP T/R | ORing_M | TDFN33-8 | AP80N04Q | 1
SI2302 | N沟道 20V/6A | Q1, Q3, Q4 | SOT23-3N | AO3400 | 3
SS8050 | 高频放大-NPN型 | Q2 | SOT23-3N | 8050-SMD | 1
100R | 贴片电阻 | R1 | R0603_L | R | 1
157K | 贴片电阻 | R2 | R0603_L | R | 1
4.7K | 贴片电阻 | R3, R6, R7 | R0603_L | R | 3
30K | 贴片电阻 | R4, R8 | R0603_L | R | 2
422K | 贴片电阻 | R5 | R0603_L | R | 1
1K | 贴片电阻 | R9, R10, R15, R16, R19, R33, R38, R40 R0603_L | | R | 8
20K | 贴片电阻 | R11, R12 | R0603_L | R | 2
2.21K | 贴片电阻 | R13, R14 | R0603_L | R | 2
10K | 贴片电阻 | R17, R18, R35, R37, R39, R41, R44, R45, R48 | R0603_L | R | 9
1mR | 贴片电阻 | R20, R21, R26 | R2512_L | R | 3
10Ω | 贴片电阻 | R22, R23, R24, R25, R27, R28 | R0603_L | R | 6
120Ω | 贴片电阻 | R29, R34 | R0603_L | R | 2
3.3K | 贴片电阻 | R30 | R0603_L | R | 1
5.6K | 贴片电阻 | R31 | R0603_L | R | 1
2K | 贴片电阻 | R32 | R0603_L | R | 1
510Ω | 贴片电阻 | R36 | R0603_L | R | 1
5.1K | 贴片电阻 | R42, R43 | R0603_L | R | 2
220R | 贴片电阻 | R46, R47, R49, R50 R0603_L | | R | 4
3x6x5 | 3x6轻触开关 | RST | SW SMD-3*6*5 | SW 3x6 | 1
NCS210RMUTAG | CURRENT SENSE AMP G=200 | S_CCAP, S_CIN, S_COUT | QFN40P140X180X6 0-10N | NCS210RMUTAG | 3
NCS20282 | 7 MHz, 125 A Low Power Operational Amplifier | S_V | BGA9C40P3X3_122X 122X62 | NCS20282 | 1
STM32G474RET6 | MCU | STM32G474 | LQFP64-10*10 | STM32G474RET6 | 1
HDR-1X4 | 4P连接器 | SWD | MX1.25-WS-4P | Header 4 | 1
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

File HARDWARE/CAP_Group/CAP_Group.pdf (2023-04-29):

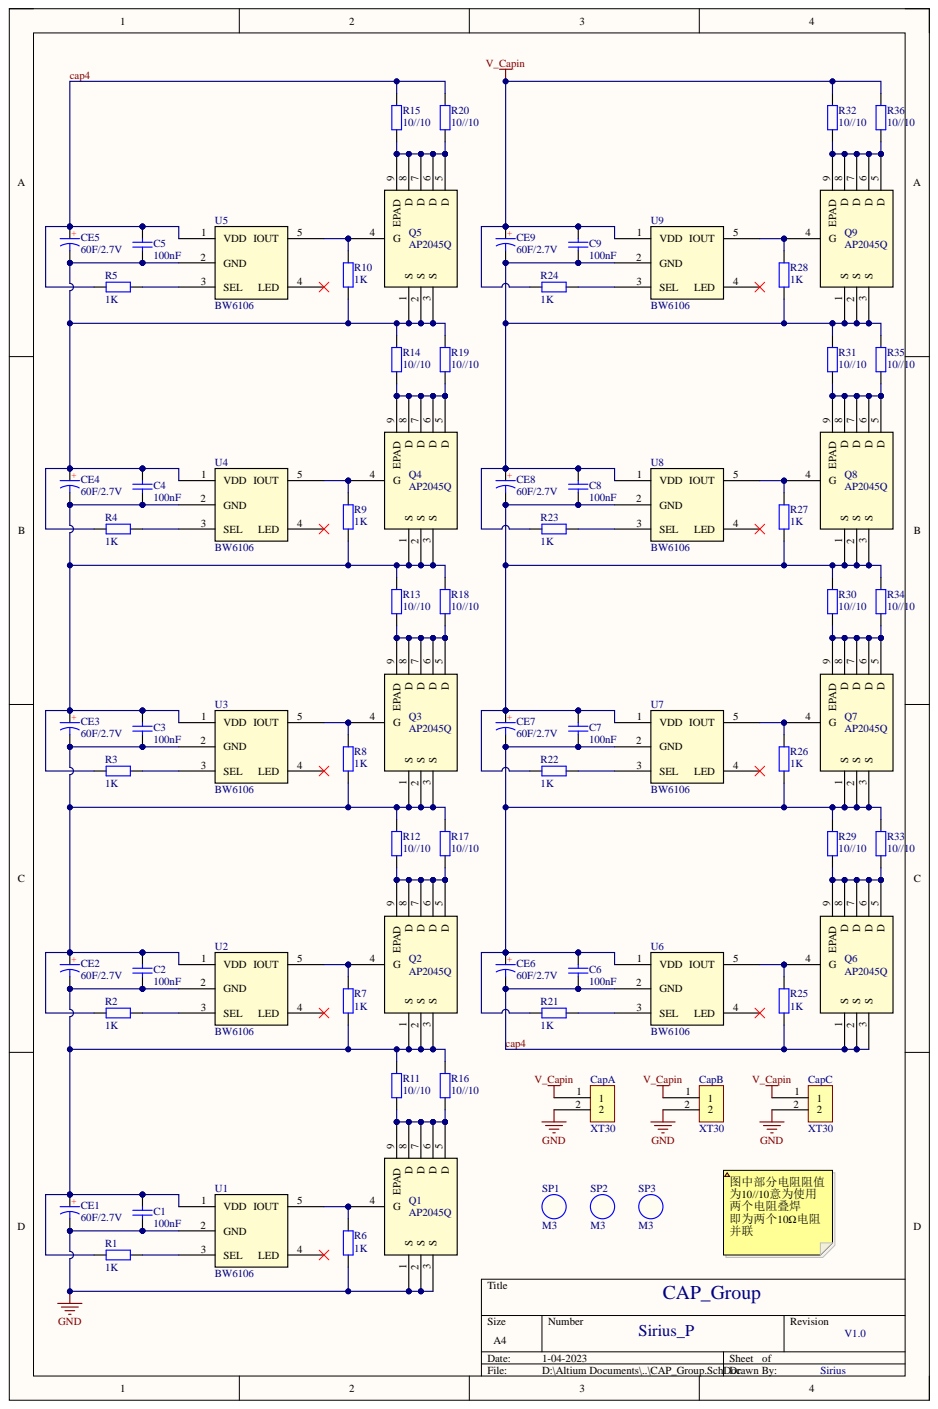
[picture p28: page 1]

60F/2.7V | | VDD 1

Date: 1-04-2023 | Sheet of
File: D:\Altium Documents\..\CAP_Group.SchDDocrawn By: | Sirius

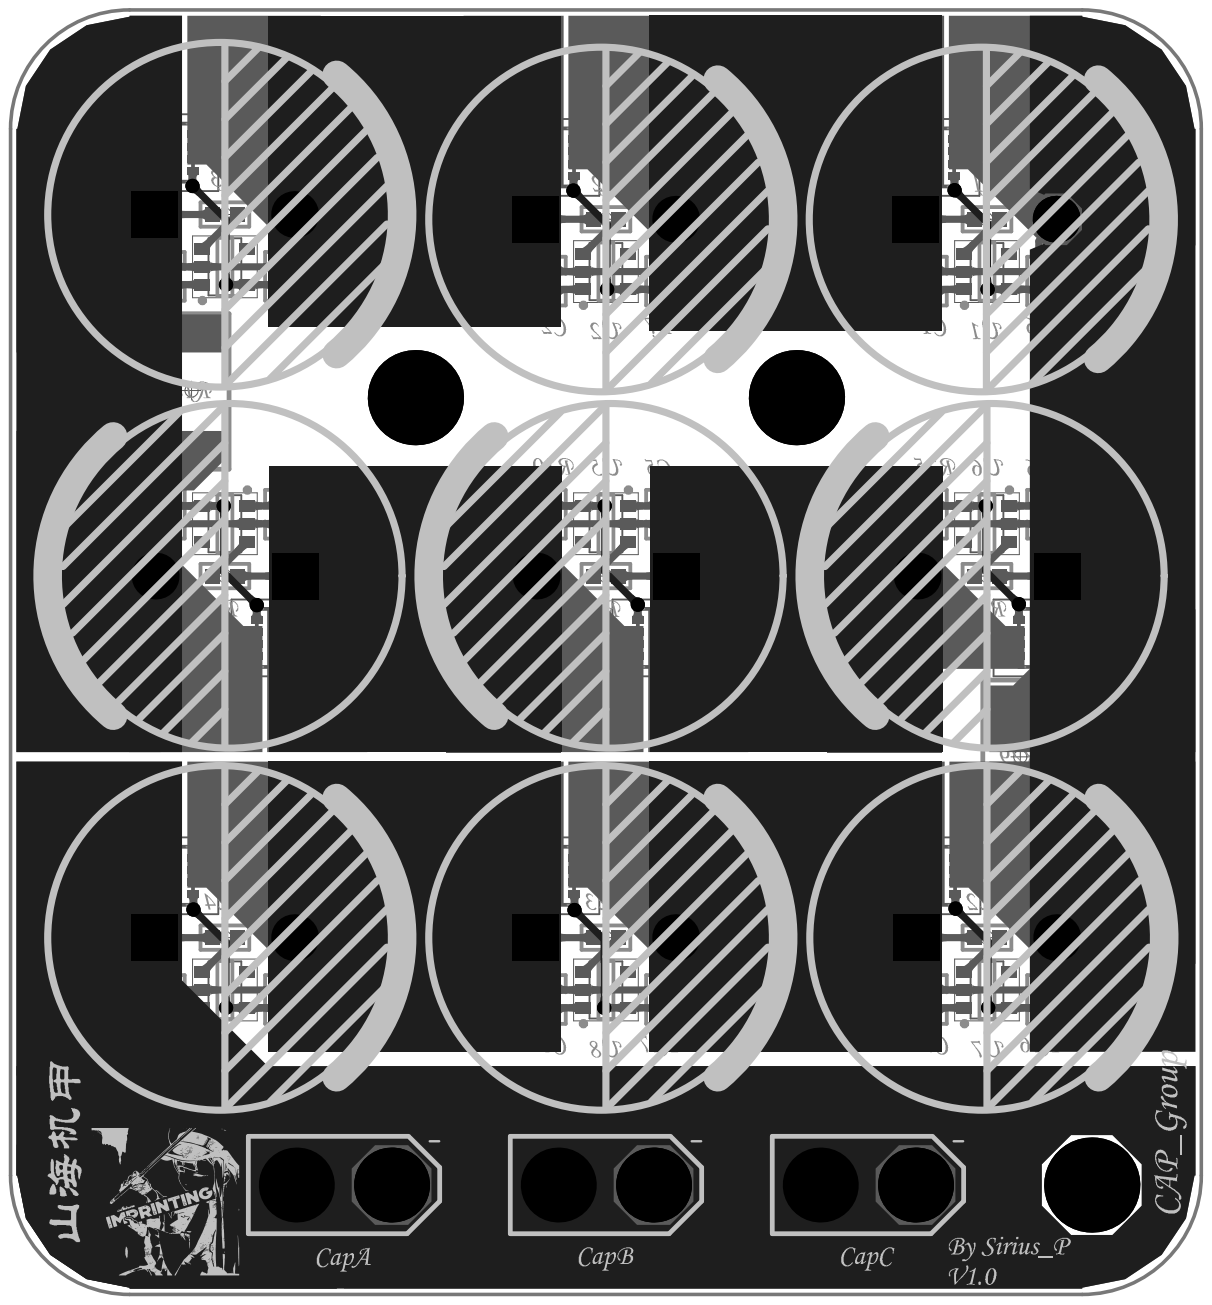
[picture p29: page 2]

Comment | Description | Designator | Footprint | LibRef | Quantity
100nF | 贴片电容 | C1, C2, C3, C4, C5, C6, C7, C8, C9 | C0603_L | C | 9
XT30 | | CapA, CapB, CapC | XT30-F | XT30 | 3
60F/2.7V | 直插电解电容 | CE1, CE2, CE3, CE4, CE5, CE6, CE7, CE8, CE9 | CE-7.5*18*35.5 - BK | CE | 9
AP2045Q | Trans MOSFET P-CH 20V 65A 8-Pin PDFN EP T/R | Q1, Q2, Q3, Q4, Q5, Q6, Q7, Q8, Q9 | TDFN33-8 | AP2045Q | 9
1K | 贴片电阻 | R1, R2, R3, R4, R5, R6, R7, R8, R9, R10, R21, R22, R23, R24, R25, R26, R27, R28 | R0603_L | R | 18
10//10 | 贴片电阻 | R11, R12, R13, R14, R15, R16, R17, R18, R19, R20, R29, R30, R31, R32, R33, R34, R35, R36 | R2512_L | R | 18
M3 | 铜柱孔 | SP1, SP2, SP3 | M3 125X200 | M3 | 3
BW6106 | 电容充电保护芯片 | U1, U2, U3, U4, U5, U6, U7, U8, U9 | SOT23-5L | BW6106 | 9

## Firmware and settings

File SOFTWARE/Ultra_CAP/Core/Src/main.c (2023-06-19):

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
/* Includes ------------------------------------------------------------------*/
#include "main.h"
#include "adc.h"
#include "dma.h"
#include "fdcan.h"
#include "fmac.h"
#include "hrtim.h"
#include "usart.h"
#include "opamp.h"
#include "spi.h"
#include "tim.h"
#include "gpio.h"

/* USER CODE BEGIN Includes */
#include "function.h"
#include "power_ctrl.h"
#include "IIR_FIlter.h"
#include "SEEKFREE_IPS114_SPI.h"
#include "CAN_receive.h"
/* USER CODE END Includes */


/* USER CODE BEGIN PV */

/* volatile is below for debug convenience */

/* USER CODE END PV */

void SystemClock_Config(void);
/* USER CODE BEGIN PFP */
#ifdef __GNUC__
/* With GCC, small printf (option LD Linker->Libraries->Small printf
 set to 'Yes') calls __io_putchar() */
#define PUTCHAR_PROTOTYPE int __io_putchar(int ch)
#else
#define PUTCHAR_PROTOTYPE int fputc(int ch, FILE *f)
#endif /* __GNUC__ */
/* USER CODE END PFP */

/**
  * @brief  The application entry point.
  * @retval int
  */
int main(void)
{
  /* MCU Configuration--------------------------------------------------------*/

  /* Reset of all peripherals, Initializes the Flash interface and the Systick. */
  HAL_Init();

  /* Configure the system clock */
  SystemClock_Config();

  /* Initialize all configured peripherals */
  MX_GPIO_Init();
  MX_DMA_Init();
  MX_FDCAN2_Init();
  MX_LPUART1_UART_Init();
  MX_USART2_UART_Init();
  MX_TIM1_Init();
  MX_ADC1_Init();
  MX_ADC2_Init();
  MX_ADC3_Init();
  MX_OPAMP2_Init();
  MX_OPAMP3_Init();
  MX_ADC4_Init();
  MX_ADC5_Init();
  MX_OPAMP5_Init();
  MX_OPAMP6_Init();
  MX_SPI3_Init();
  MX_SPI2_Init();
  MX_TIM2_Init();
  MX_HRTIM1_Init();
  MX_OPAMP1_Init();
  MX_FMAC_Init();
  MX_FDCAN1_Init();
  /* USER CODE BEGIN 2 */

    /*OD pin down to disable abnormal operations*/
    HAL_GPIO_WritePin(R_OD_GPIO_Port, R_OD_Pin, GPIO_PIN_RESET);
    HAL_GPIO_WritePin(L_OD_GPIO_Port, L_OD_Pin, GPIO_PIN_RESET);

    /*open peripheral driver*/
    OPAMP_Start();
    ADC_Calib_Start();
    TIM1_PWM_Init();
    ips114_init();
    can_filter_init();
    HAL_FMAC_FilterConfig_my();
    power_init();

    /*initial finished*/
    printf("\n\r init complete\n\r");
    htim1.Instance->CCR1 = 0;
    htim1.Instance->CCR2 = 0;
    htim1.Instance->CCR3 = 0;
    htim1.Instance->CCR4 = 0;

    /*open timer interrupt*/
    HAL_TIM_Base_Start_IT(&htim2); //5mS interrupt
    HRTIM_Init();

    /*calibration function, calibration is defined in main.h*/
#if calibration == 1
//    HAL_GPIO_WritePin(L_OD_GPIO_Port, L_OD_Pin, GPIO_PIN_SET);
//    HAL_GPIO_WritePin(R_OD_GPIO_Port, R_OD_Pin, GPIO_PIN_SET);
    HRTIM_DMA_Buffer[0] = (uint16_t)(0.95 * HRTIMB_Period);//BUCK duty
    HRTIM_DMA_Buffer[1] = (uint16_t)(0.95 * HRTIMB_Period) >> 1;//ADC sampling trigger
    HRTIM_DMA_Buffer[2] = MIN_REG_VALUE;//Boost duty
    HRTIM_DMA_Buffer[3] = (uint16_t)(0.96 * HRTIMA_Period);
#endif

  /* USER CODE END 2 */

  /* Infinite loop */
  /* USER CODE BEGIN WHILE */
    while (1)
    {
        printf("power_in=%f\r\n", in.P);
        printf("v_in=%f\r\n", in.V);
        printf("c_in=%f\r\n", in.I);
        printf("v_cap=%f\r\n", cap.V);
        printf("c_cap=%f\r\n", cap.I);
        printf("c_chassis=%f\r\n", c_chassis.value_elec);
//        printf("full_bridge_in=%f\r\n", full_bridge_in.I);
        printf("\r\n");

//        if (IPSShowCnt > 60) //300m flash once ips
//        {
//            IPSShowCnt = 0;
//            ips_usrdisplay();
//        }

        if (CANSendCnt > 19) //100m send once
        {
            CANSendCnt = 0;
            CAN_cmd_powerctrl();
        }
    /* USER CODE END WHILE */

    /* USER CODE BEGIN 3 */
    }
  /* USER CODE END 3 */
}

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
/* USER CODE BEGIN 4 */

/**
 * @brief  Retargets the C library printf function to the USART.
 * @param  None
 * @retval None
 */
PUTCHAR_PROTOTYPE
{
    /* Place your implementation of fputc here */
    /* e.g. write a character to the LPUART1 and Loop until the end of transmission */
    HAL_UART_Transmit(&hlpuart1, (uint8_t *) &ch, 1, 0xFFFF);

    return ch;
}

/* USER CODE END 4 */
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


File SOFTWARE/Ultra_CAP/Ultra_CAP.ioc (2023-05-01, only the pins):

Mcu.UserName=STM32G474RETx
PA1.GPIO_Label=c_in
PA1.Signal=SharedAnalog_PA1
PA10.Signal=HRTIM1_CHB1
PA11.Signal=USB_DM
PA12.Signal=USB_DP
PA13.Signal=SYS_JTMS-SWDIO
PA14.Signal=SYS_JTCK-SWCLK
PA2.Signal=LPUART1_TX
PA3.Signal=LPUART1_RX
PA4.GPIO_Label=EC11_A
PA4.Signal=GPXTI4
PA5.GPIO_Label=EC11_B
PA5.Signal=GPXTI5
PA6.GPIO_Label=EC11_K
PA6.Signal=GPXTI6
PA7.GPIO_Label=c_cap
PA7.Signal=OPAMP2_VINP
PA8.Signal=HRTIM1_CHA1
PA9.GPIO_Label=L_OD
PA9.Signal=GPIO_Output
PB0.GPIO_Label=c_chassis
PB0.Signal=OPAMP3_VINP
PB11.GPIO_Label=IPS114_REST
PB11.Signal=GPIO_Output
PB12.GPIO_Label=v_in
PB12.Signal=OPAMP6_VINP
PB13.GPIO_Label=IPS114_SCL
PB13.Signal=SPI2_SCK
PB14.GPIO_Label=v_cap
PB14.Signal=OPAMP5_VINP
PB15.GPIO_Label=IPS114_SDA
PB15.Signal=SPI2_MOSI
PB3.Signal=USART2_TX
PB4.Signal=USART2_RX
PB5.Signal=FDCAN2_RX
PB6.Signal=FDCAN2_TX
PB8-BOOT0.Signal=FDCAN1_RX
PB9.Signal=FDCAN1_TX
PC0.GPIO_Label=Beep
PC0.Signal=S_TIM1_CH1
PC1.GPIO_Label=RGB_R
PC1.Signal=S_TIM1_CH2
PC10.GPIO_Label=GYRO_SCK
PC10.Signal=SPI3_SCK
PC11.GPIO_Label=GYRO_MISO
PC11.Signal=SPI3_MISO
PC12.GPIO_Label=GYRO_MOSI
PC12.Signal=SPI3_MOSI
PC2.GPIO_Label=RGB_G
PC2.Signal=S_TIM1_CH3
PC3.GPIO_Label=RGB_B
PC3.Signal=S_TIM1_CH4
PC6.GPIO_Label=IPS114_DC
PC6.Signal=GPIO_Output
PC7.GPIO_Label=IPS114_CS
PC7.Signal=GPIO_Output
PC8.GPIO_Label=IPS114_BL
PC8.Signal=GPIO_Output
PC9.GPIO_Label=R_OD
PC9.Signal=GPIO_Output
PD2.GPIO_Label=GYRO_CS
PD2.Signal=GPIO_Output
PF0-OSC_IN.Signal=RCC_OSC_IN

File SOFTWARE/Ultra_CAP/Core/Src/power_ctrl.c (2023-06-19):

#include "power_ctrl.h"
#include "function.h"
#include "pid.h"
#include "filter.h"
#include "IIR_FIlter.h"

ELEC_INFO_STRUCT c_in;      //current in
ELEC_INFO_STRUCT c_cap;     //current cap
ELEC_INFO_STRUCT c_chassis; //current chassis
ELEC_INFO_STRUCT v_in;      //voltage in
ELEC_INFO_STRUCT v_cap;     //voltage cap

CCMRAM CONTROL_STRUCT in, chassis, full_bridge_in, cap;
//     BAT_input output_chassis dcdc_input dcdc_output(cap)

volatile fp32 pid_final = 0;
volatile fp32 capIcalc = 0;

volatile uint16_t HRTIM_DMA_Buffer[4] = { 0, 12920, 100, 25840 };
//                             buck_duty adc_duty boostup_duty boostdown_duty

/*Linear calibration once*/
void ADC_Linear_calibration_init(ELEC_INFO_STRUCT *p, fp32 real1, fp32 get1, fp32 real2, fp32 get2)
{
    fp64 a, b;
    p->get_volt1 = get1;
    p->get_volt2 = get2;
    p->real_value1 = real1;
    p->real_value2 = real2;
    if ((p->get_volt2 - p->get_volt1 == 0) || (p->real_value2 - p->real_value1 == 0))
    {
        return;
    }

    a = (p->real_value2 - p->real_value1) / (p->get_volt2 - p->get_volt1);
    b = (p->real_value1 - p->get_volt1 * a);

    p->ratio = a * p->ratio;
    p->offset = b;
}

/*change adc value to elec(A, V)*/
CCMRAM void ADC_value_to_elec(ELEC_INFO_STRUCT *p)
{
    p->value_elec = (p->value_origin) * p->ratio + p->offset;
}

/*power control function init*/
void power_init(void)
{
    /*V_Gain is (2.21K + 20 K) / 2.21K*/
    v_in.elec_type = 0;
    v_in.ratio = (10.0f * VDDA) / ADC_Maxvalue;
    v_in.offset = 0;
    v_cap.elec_type = 0;
    v_cap.ratio = (10.0f * VDDA) / ADC_Maxvalue;
    v_cap.offset = 0;

    /*I_Gain is 1 / (1m * 200)*/
    c_in.elec_type = 1;
    c_in.ratio = (VDDA * 5.0f) / ADC_Maxvalue;
    c_in.offset = 0;
    c_cap.elec_type = 1;
    c_cap.ratio = (VDDA * 5.0f) / ADC_Maxvalue;
    c_cap.offset = 0;
    c_chassis.elec_type = 1;
    c_chassis.ratio = (VDDA * 5.0f) / ADC_Maxvalue;
    c_chassis.offset = 0;

#define PARA_CAL_ENABLE (1) //elec_calibration: 0 -> disable; 1 -> enable
#define board_num (4)       //board series num
#define LPF_ENABLE (0)      //low pass filter: 0 -> disable; 1 -> enable

#if PARA_CAL_ENABLE == 1

#if board_num == 1 //finished
    ADC_Linear_calibration_init(&c_in, 1.004f, 1.361905f, 8.0f, 11.161173f);
    ADC_Linear_calibration_init(&c_cap, 1.0f, 1.35f, 8.01f, 10.56f);
    ADC_Linear_calibration_init(&c_chassis, 1.0f, 1.42f, 8.0f, 11.1f);
#endif
#if board_num == 2 //have to finish
    ADC_Linear_calibration_init(&c_in, 1.005f, 1.56f, 8.003f, 12.3f);
    ADC_Linear_calibration_init(&c_cap, 1.012f, 1.33f, 7.99f, 10.32f);
    ADC_Linear_calibration_init(&c_chassis, 1.0f, 1.45f, 7.99f, 10.95f);
#endif
#if board_num == 3 //finished
    ADC_Linear_calibration_init(&c_in, 1.006f, 1.535165f, 8.004f, 12.16f);
    ADC_Linear_calibration_init(&c_cap, 1.0f, 1.35f, 7.99f, 10.25f);
    ADC_Linear_calibration_init(&c_chassis, 1.0f, 1.4f, 7.99f, 10.77f);
#endif
#if board_num == 4 //finished
    ADC_Linear_calibration_init(&c_in, 1.006f, 1.482784f, 8.006f, 11.95f);
    ADC_Linear_calibration_init(&c_cap, 1.0f, 1.34f, 7.99f, 10.14f);
    ADC_Linear_calibration_init(&c_chassis, 1.0f, 1.39f, 7.99f, 10.71f);
#endif

#endif

    /*PID init is in function BuckBoostVLoopCtlPID*/
//    PID_init(&voltageout_loop, 0.03f, 450.0f / 200000.0f, 0.000008f * 200000.0f, 0.95, 1, 0, -1); //voltage loop
//    PID_init(&voltageout_loop, 0.0164f, 76.0f / 200000.0f, 0.00000647f * 200000.0f, 0.53, 1, 0, -1); //voltage loop
//    PID_init(&currentout_loop, 0.006f, 22.0f / 200000.0f, 0.0f * 200000.0f, 0.95, 1, 0, -1); //current loop
//    PID_init(&powerin_loop, 0.0042f, 5.627f / 200000.0f, 0.0f * 200000.0f, 0.95, 1, 0, -1);   //power loop
//    PID_init(&power_referee_loop, 0.3,0.05f,0, 120, 50, -120, -50);
    /*LPF init*/
#if LPF_ENABLE == 1
    for (char i = 0; i < 5; i++)
    {
        low_filter_init(&lpf[i], 200e3, 30e3);
    }
#endif

}

/*ADC sample function*/
CCMRAM void ADCSample(void)
{

    ADC_value_to_elec(&c_cap);
    ADC_value_to_elec(&c_chassis);
    ADC_value_to_elec(&v_in);
    ADC_value_to_elec(&v_cap);

    //ADC c_in calculate is last to wait for FMAC finish
    ADC_value_to_elec(&c_in);

    //sample has 0 shift,use 0 when sample num are too small
    if (v_cap.value_elec <= 0.1f)
    {
        v_cap.value_elec = 0.1f;  //prevent from dividing 0
    }

    /*ADC sampling filtered in ADC peripheral's internal adder and shifter to release CPU load*/
#if LPF_ENABLE == 1
//    lpf[0].Input = c_in.value_elec;
//    lpf[1].Input = in.V * in.I;
//    lpf[1].Input = v_in.value_elec;
//    lpf[2].Input = v_cap.value_elec;
//    lpf[3].Input = c_cap.value_elec;
//    lpf[4].Input = c_chassis.value_elec;

//    for (char i = 0; i < 5; i++)
//    {
//        low_filter_calc(&lpf[i]);
//    }

    in.V = v_in.value_elec;
    in.I = c_in.value_elec;

    /*power in filter*/
    lpf[1].Input = in.V * in.I;
    low_filter_calc(&lpf[1]);
    in.P = lpf[1].Output;
    in.P = in.V * in.I;

    full_bridge_in.I = c_in.value_elec - c_chassis.value_elec;
    cap.V = v_cap.value_elec;

    /*calculate cap current*/
    capIcalc = (in.V / cap.V) * full_bridge_in.I * 1.1f;

    if (capIcalc >= 1.0f)
    {
        cap.I = c_cap.value_elec;
    }
    else
    {
        cap.I = capIcalc;
    }
    cap.P = cap.V * cap.I;

#else
    in.V = v_in.value_elec;
    in.I = c_in.value_elec;
    in.P = in.V * in.I;

    full_bridge_in.I = c_in.value_elec - c_chassis.value_elec;

    cap.V = v_cap.value_elec;

    /*calculate cap current*/
    capIcalc = (in.V / cap.V) * full_bridge_in.I * 1.1f;

    if (capIcalc >= 0.5f)
    {
        cap.I = c_cap.value_elec;
    }
    else
    {
        cap.I = capIcalc;
    }

//    full_bridge_in.V = in.V;
//    full_bridge_in.P = full_bridge_in.V * full_bridge_in.I;
//    cap.P = cap.V * cap.I;
#endif
}
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

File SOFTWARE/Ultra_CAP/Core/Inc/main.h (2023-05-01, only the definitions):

#define ccmram_enable (1)
#define CCMRAM __attribute__((section("ccmram")))
#define CCMRAM /**/
#define HRTIMB_Period 27200
#define HRTIMA_Period 27200
#define HRTIMMaster_Period 27200
#define Beep_Pin GPIO_PIN_0
#define Beep_GPIO_Port GPIOC
#define RGB_R_Pin GPIO_PIN_1
#define RGB_R_GPIO_Port GPIOC
#define RGB_G_Pin GPIO_PIN_2
#define RGB_G_GPIO_Port GPIOC
#define RGB_B_Pin GPIO_PIN_3
#define RGB_B_GPIO_Port GPIOC
#define c_in_Pin GPIO_PIN_1
#define c_in_GPIO_Port GPIOA
#define EC11_A_Pin GPIO_PIN_4
#define EC11_A_GPIO_Port GPIOA
#define EC11_B_Pin GPIO_PIN_5
#define EC11_B_GPIO_Port GPIOA
#define EC11_K_Pin GPIO_PIN_6
#define EC11_K_GPIO_Port GPIOA
#define c_cap_Pin GPIO_PIN_7
#define c_cap_GPIO_Port GPIOA
#define c_chassis_Pin GPIO_PIN_0
#define c_chassis_GPIO_Port GPIOB
#define IPS114_REST_Pin GPIO_PIN_11
#define IPS114_REST_GPIO_Port GPIOB
#define v_in_Pin GPIO_PIN_12
#define v_in_GPIO_Port GPIOB
#define IPS114_SCL_Pin GPIO_PIN_13
#define IPS114_SCL_GPIO_Port GPIOB
#define v_cap_Pin GPIO_PIN_14
#define v_cap_GPIO_Port GPIOB
#define IPS114_SDA_Pin GPIO_PIN_15
#define IPS114_SDA_GPIO_Port GPIOB
#define IPS114_DC_Pin GPIO_PIN_6
#define IPS114_DC_GPIO_Port GPIOC
#define IPS114_CS_Pin GPIO_PIN_7
#define IPS114_CS_GPIO_Port GPIOC
#define IPS114_BL_Pin GPIO_PIN_8
#define IPS114_BL_GPIO_Port GPIOC
#define R_OD_Pin GPIO_PIN_9
#define R_OD_GPIO_Port GPIOC
#define L_OD_Pin GPIO_PIN_9
#define L_OD_GPIO_Port GPIOA
#define GYRO_SCK_Pin GPIO_PIN_10
#define GYRO_SCK_GPIO_Port GPIOC
#define GYRO_MISO_Pin GPIO_PIN_11
#define GYRO_MISO_GPIO_Port GPIOC
#define GYRO_MOSI_Pin GPIO_PIN_12
#define GYRO_MOSI_GPIO_Port GPIOC
#define GYRO_CS_Pin GPIO_PIN_2
#define GYRO_CS_GPIO_Port GPIOD
#define calibration (0) //calibration function

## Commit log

2023-04-29 initial Prj
    [CAP_Group.PrjPcb, CAP_Group.SchDoc, Digital.SchDoc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]
2023-04-30 update tired
2023-05-01 update readme&pdf&HARDWARE
    [Power.SchDoc, Ultra_CAP.PrjPcb]
2023-05-31 update sch
    [Power.SchDoc, Ultra_CAP.PrjPcb]

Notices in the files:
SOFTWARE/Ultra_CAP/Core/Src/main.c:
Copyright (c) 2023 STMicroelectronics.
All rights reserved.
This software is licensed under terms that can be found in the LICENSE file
